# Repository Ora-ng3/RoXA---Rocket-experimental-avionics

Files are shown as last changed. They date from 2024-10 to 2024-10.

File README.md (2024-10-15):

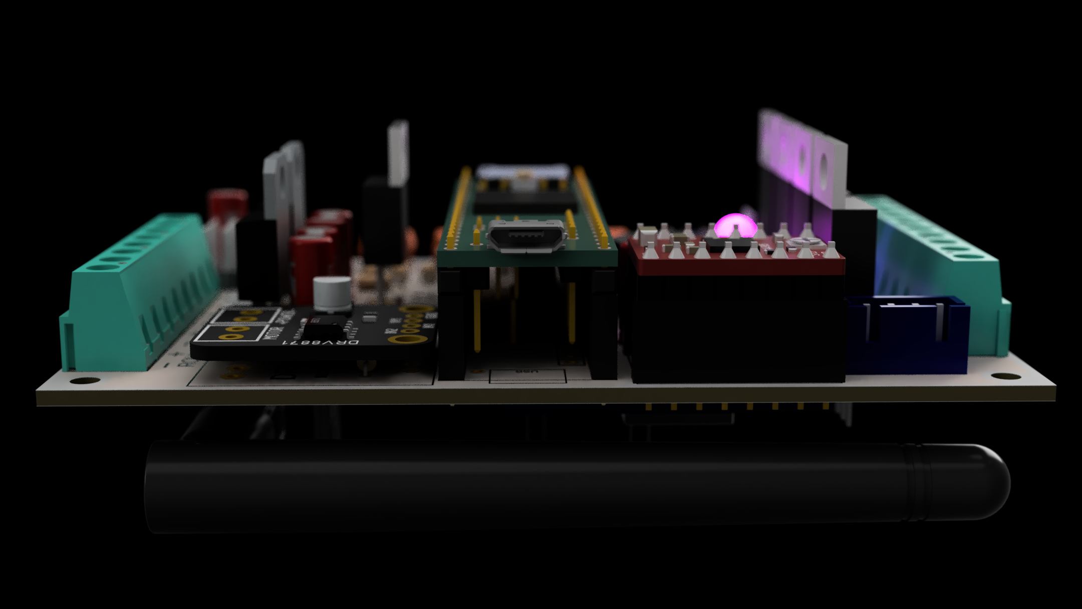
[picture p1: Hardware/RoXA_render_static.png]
The RoXA Flight Computer


RoXA stands for Rocket experimental avionics. It's my first flight computer (that is more than an arduino with a barometer soldered : ), you can see in [this instructables](https://www.instructables.com/Rocket-Flight-Computer/) a more detailed description of the design and build.

In this repo you'll find the PCB design and manufacturing files, as well as the code. For now it can reliably trigger first and second events. I'm working actively on this project to add reliable data logging and telemetry (and many other things...).

The RoXA Flight Computer

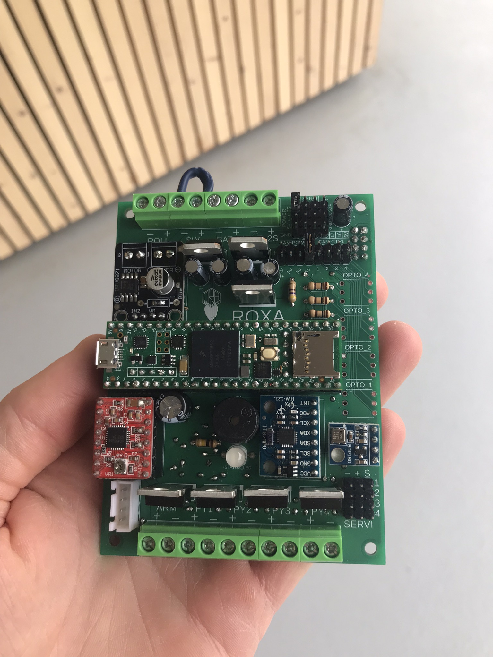
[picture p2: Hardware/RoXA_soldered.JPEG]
The RoXA Flight Computer


Keywords : Flight computer avionics Rocket Reaction wheel Rogallo

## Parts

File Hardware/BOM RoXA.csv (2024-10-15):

Qty | Device | Value | Parts | Unit Price | Price
1 | Microcontroller | Teensy 4.1 | U$1 | 40,00 € | 40,00 €
1 | Barometer | GY-68 BMP180 | U$4 | 2,00 € | 2,00 €
1 | IMU | GY-521 MPU6050 | U1 | 2,50 € | 2,50 €
1 | GPS | GY-NEO6MV2 | U$3 | 10,00 € | 10,00 €
1 | Radio Module | NRF24L01+PA+LNA | U$2 | 4,00 € | 4,00 €
1 | Motor Driver | DRV8871 | U$5 | 8,00 € | 8,00 €
1 | Stepper Driver | A4988 | U$6 | 2,00 € | 2,00 €
1 | RGB Led | 5mm Com. Cat. | STATUS_LED | 0,10 € | 0,10 €
1 | Buzzer | 3.3V 12mm | U$7 | 1,00 € | 1,00 €
2 | 5V Regulator | L7805CV TO220V | CAM_5V_REG, MAIN_5V_REG | 0,80 € | 1,60 €
5 | N-Mosfet | IRFZ44N TO220V | CAM_FET, PYFET1, PYFET2, PYFET3, PYFET4 | 0,80 € | 4,00 €
15 | Resistor | 100k | R2, R3, R4, R8, R9, R10, R14, R15, R16, R20, R21, R22, R26, R27, R28 | 0,05 € | 0,75 €
4 | Resistor | 1ohm | R5, R11, R17, R23 | 0,05 € | 0,20 €
1 | Resistor | 10ohm | R31 | 0,05 € | 0,05 €
2 | Resistor | 68ohm | R29, R30 | 0,05 € | 0,10 €
4 | Resistor | 100ohm | R33, R34, R35, R36 | 0,05 € | 0,20 €
5 | Resistor | 470ohm | R6, R12, R18, R24, R32 | 0,05 € | 0,25 €
5 | Resistor | 1M | R1, R7, R13, R19, R25 | 0,05 € | 0,25 €
2 | Capacitor | 1µF | C2, C7 | 0,15 € | 0,30 €
4 | Capacitor | 10µF | C1, C4, C5, C6 | 0,15 € | 0,60 €
1 | Capacitor | 100µF | C3 | 0,15 € | 0,15 €
4 | Optocoupler | 4N28 | OPTO_1, OPTO_2, OPTO_3, OPTO_4 | 0,15 € | 0,60 €
8 | Headers | 2 pins | CAM_BREAKOUTS | 0,01 € | 0,08 €
4 | Headers | 3 pins | SERVO_HD_1, SERVO_HD_2, SERVO_HD_3, SERVO_HD_4 | 0,01 € | 0,04 €
4 | Headers | 4 pins | POWER_BK | 0,01 € | 0,04 €
1 | Stepper connector | 4 pins JST XH | STEPPER_BK | 0,10 € | 0,10 €
9 | Screw terminals | 2 pins 5mm | ARM, BATT, BAT_2S, PY1, PY2, PY3, PY4, ROLL, SW | 0,10 € | 0,90 €
1 | PCB Board |  |  | 2,00 € | 2,00 €
 |  |  |  | Total : | 81,81 €

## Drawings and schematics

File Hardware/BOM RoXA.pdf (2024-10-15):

### BOM ROXA

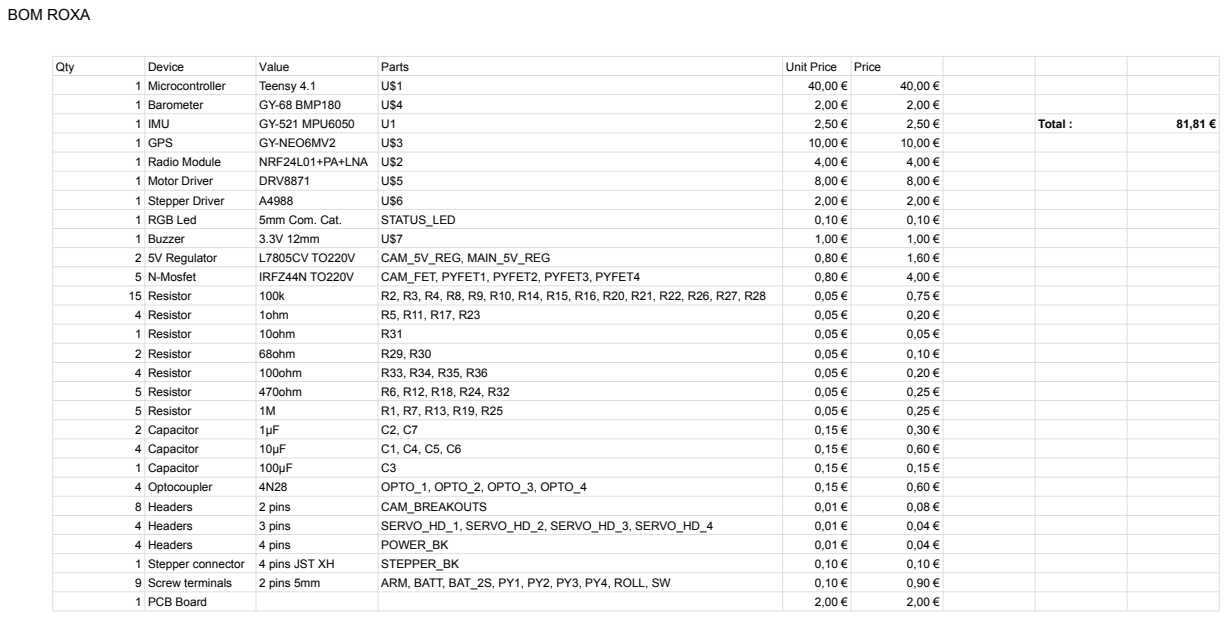
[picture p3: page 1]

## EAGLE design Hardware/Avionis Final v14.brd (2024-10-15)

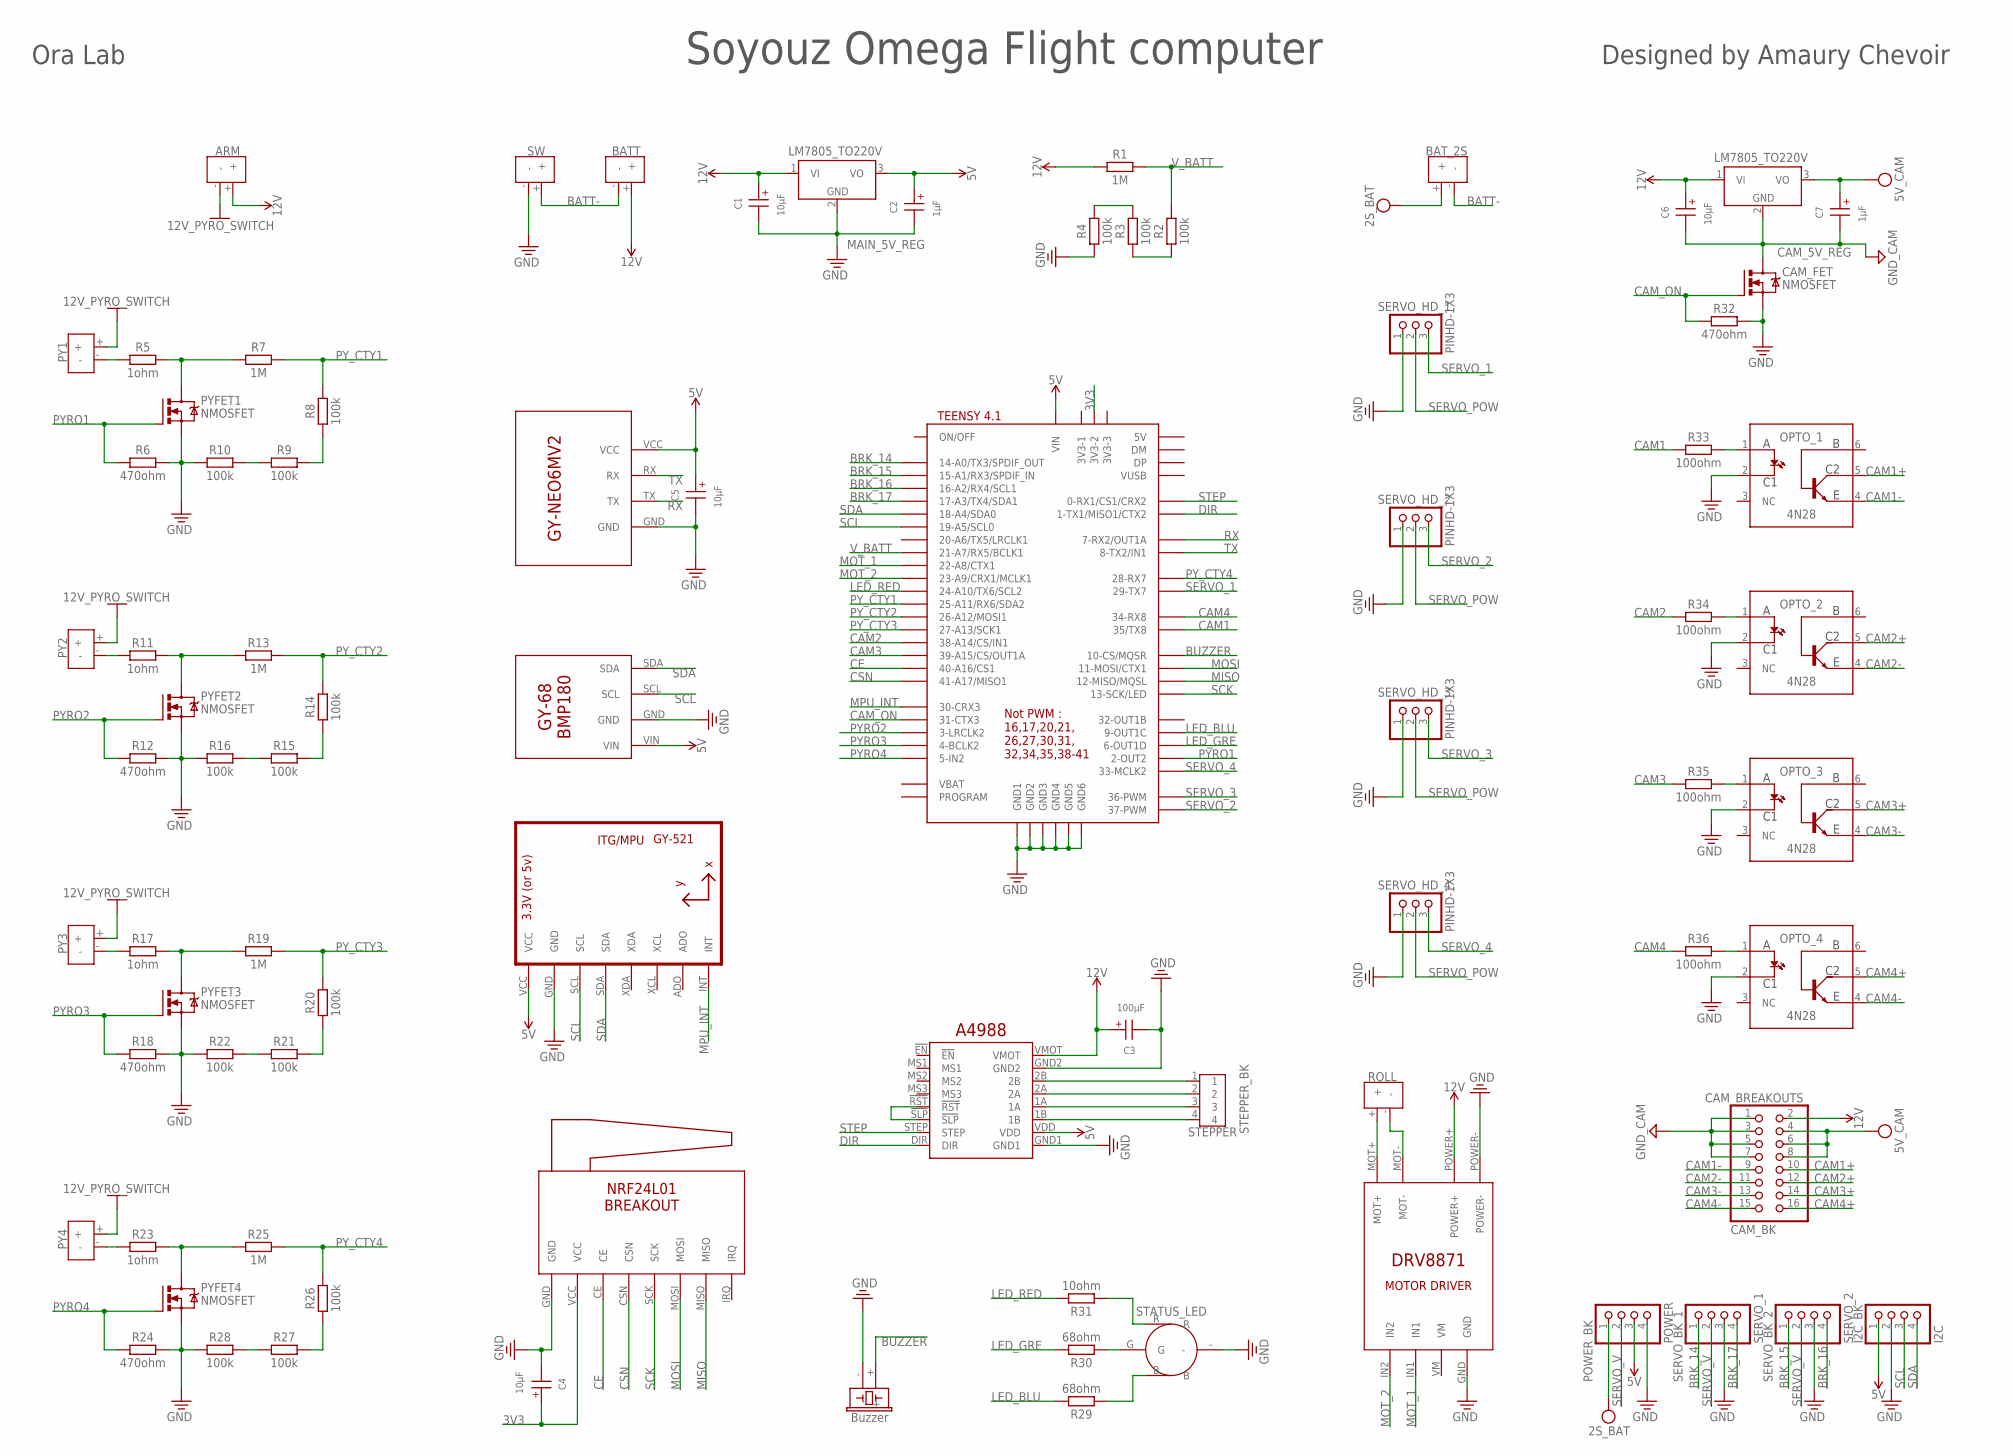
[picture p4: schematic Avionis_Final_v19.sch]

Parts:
ARM: TERMBLK_2; TERMBLK_2_LOW
BATT: TERMBLK_2; TERMBLK_2_LOW
BAT_2S: TERMBLK_2; TERMBLK_2_LOW
C1, C4, C5, C6: 10µF; WCAP-AT1H_5X11(DXL)
C2, C7: 1µF; WCAP-AT1H_5X11(DXL)
C3: 100µF; WCAP-AT1H_5X11(DXL)
CAM_5V_REG: LM7805_TO220V; TO220V
CAM_BREAKOUTS: CAM_BK; 2X08
CAM_FET: NMOSFET; TO220BV
I2C_BK: I2C; 1X04
MAIN_5V_REG: LM7805_TO220V; TO220V
OPTO_1, OPTO_2, OPTO_3, OPTO_4: 4N28; DIP762W60P254L712H480Q6B
POWER_BK: POWER; 1X04
PY1, PY2, PY3, PY4: TERMBLK_2; TERMBLK_2_LOW
PYFET1, PYFET2, PYFET3, PYFET4: NMOSFET; TO220BV
R1, R7, R13, R19, R25: 1M; RESAD724W46L381D178B
R2, R3, R4, R8, R9, R10, R14, R15, R16, R20, R21, R22, R26, R27, R28: 100k; RESAD724W46L381D178B
R5, R11, R17, R23: 1ohm; RESAD724W46L381D178B
R6, R12, R18, R24, R32: 470ohm; RESAD724W46L381D178B
R29, R30: 68ohm; RESAD724W46L381D178B
R31: 10ohm; RESAD724W46L381D178B
R33, R34, R35, R36: 100ohm; RESAD724W46L381D178B
ROLL: TERMBLK_2; TERMBLK_2_LOW
SERVO_BK_1: SERVO_1; 1X04
SERVO_BK_2: SERVO_2; 1X04
SERVO_HD_1, SERVO_HD_2, SERVO_HD_3, SERVO_HD_4: PINHD-1X3; 1X03
STATUS_LED: LED_RGB_CAT_THT
STEPPER_BK: STEPPER; B4B-XH-A
SW: TERMBLK_2; TERMBLK_2_LOW
U1: GY-521MPU6050; GY-521
U$1: TEENSY41-E; TENNSY41-E
U$2: NRF24L01_BREAKOUT
U$3: GY-NEO6MV2
U$4: GY-68_BMP180
U$5: DRV8871_MOTORDRIVER
U$6: A4988
U$7: BUZZER_12MM; BUZZER-12MM-KIT

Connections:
1A: STEPPER_BK.3, U$6.1A
1B: STEPPER_BK.4, U$6.1B
2A: STEPPER_BK.2, U$6.2A
2B: STEPPER_BK.1, U$6.2B
2S_BAT: BAT_2S.+, POWER_BK.1
3V3: C4.1 (+), U$1.3V3-2, U$2.VCC
5V: C2.1 (+), C5.1 (+), I2C_BK.1, MAIN_5V_REG.3 (VO), POWER_BK.3, U1.VCC, U$1.VIN, U$3.VCC, U$4.VIN, U$6.VDD
5V_CAM: C7.1 (+), CAM_5V_REG.3 (VO), CAM_BREAKOUTS.4, CAM_BREAKOUTS.6, CAM_BREAKOUTS.8
12V: ARM.+, BATT.+, C1.1 (+), C3.1 (+), C6.1 (+), CAM_5V_REG.1 (VI), CAM_BREAKOUTS.2, MAIN_5V_REG.1 (VI), R1.1, U$5.POWER+, U$6.VMOT
12V_PYRO_SWITCH: ARM.-, PY1.+, PY2.+, PY3.+, PY4.+
!RST: U$6.!RST, U$6.!SLP
BATT-: BATT.-, BAT_2S.-, SW.+
BRK_14: SERVO_BK_1.1, U$1.14-A0/TX3/SPDIF_OUT
BRK_15: SERVO_BK_2.1, U$1.15-A1/RX3/SPDIF_IN
BRK_16: SERVO_BK_2.4, U$1.16-A2/RX4/SCL1
BRK_17: SERVO_BK_1.4, U$1.17-A3/TX4/SDA1
BUZZER: U$1.10-CS\MQSR (10-CS/MQSR), U$7.+
CAM1: R33.1, U$1.35-TX8 (35/TX8)
CAM1+: CAM_BREAKOUTS.10, OPTO_1.5 (C2)
CAM1-: CAM_BREAKOUTS.9, OPTO_1.4 (E)
CAM2: R34.1, U$1.38-A14/CS/IN1
CAM2+: CAM_BREAKOUTS.12, OPTO_2.5 (C2)
CAM2-: CAM_BREAKOUTS.11, OPTO_2.4 (E)
CAM3: R35.1, U$1.39-A15/CS/OUT1A
CAM3+: CAM_BREAKOUTS.14, OPTO_3.5 (C2)
CAM3-: CAM_BREAKOUTS.13, OPTO_3.4 (E)
CAM4: R36.1, U$1.34-RX8
CAM4+: CAM_BREAKOUTS.16, OPTO_4.5 (C2)
CAM4-: CAM_BREAKOUTS.15, OPTO_4.4 (E)
CAM_ON: CAM_FET.G, R32.1, U$1.31-CTX3
CE: U$1.40-A16/CS1, U$2.CE
CSN: U$1.41-A17/MISO1, U$2.CSN
DIR: U$1.1-TX1/MISO1/CTX2, U$6.DIR
GND: C1.2 (-), C2.2 (-), C3.2 (-), C4.2 (-), C5.2 (-), CAM_FET.S, I2C_BK.2, MAIN_5V_REG.2 (GND), OPTO_1.2 (C1), OPTO_2.2 (C1), OPTO_3.2 (C1), OPTO_4.2 (C1), POWER_BK.4, PYFET1.S, PYFET2.S, PYFET3.S, PYFET4.S, R4.1, R6.2, R10.1, R12.2, R16.1, R18.2, R22.1, R24.2, R28.1, R32.2, SERVO_BK_1.3, SERVO_BK_2.3, SERVO_HD_1.1, SERVO_HD_2.1, SERVO_HD_3.1, SERVO_HD_4.1, STATUS_LED.-, SW.-, U1.GND, U$1.GND1, U$1.GND2, U$1.GND3, U$1.GND4, U$1.GND5, U$1.GND6, U$2.GND, U$3.GND, U$4.GND, U$5.GND, U$5.POWER-, U$6.GND1, U$6.GND2, U$7.-
GND_CAM: C6.2 (-), C7.2 (-), CAM_5V_REG.2 (GND), CAM_BREAKOUTS.1, CAM_BREAKOUTS.3, CAM_BREAKOUTS.5, CAM_BREAKOUTS.7, CAM_FET.D
LED_BLU: R29.2, U$1.9-OUT1C
LED_GRE: R30.2, U$1.6-OUT1D
LED_RED: R31.2, U$1.24-A10/TX6/SCL2
MISO: U$1.12-MISO/MQSL, U$2.MISO
MOSI: U$1.11-MOSI/CTX1, U$2.MOSI
MOT_1: U$1.22-A8/CTX1, U$5.IN1
MOT_2: U$1.23-A9/CRX1/MCLK1, U$5.IN2
MPU_INT: U1.INT, U$1.30-CRX3
unnamed: ROLL.+, U$5.MOT+
unnamed: ROLL.-, U$5.MOT-
unnamed: PY2.-, R11.1
unnamed: PYFET2.D, R11.2, R13.1
unnamed: R15.1, R16.2
unnamed: R14.1, R15.2
unnamed: PY3.-, R17.1
unnamed: PY1.-, R5.1
unnamed: R9.1, R10.2
unnamed: PYFET1.D, R5.2, R7.1
unnamed: R2.1, R3.1
unnamed: R3.2, R4.2
unnamed: R8.1, R9.2
unnamed: PYFET3.D, R17.2, R19.1
unnamed: R21.1, R22.2
unnamed: R20.1, R21.2
unnamed: PY4.-, R23.1
unnamed: PYFET4.D, R23.2, R25.1
unnamed: R27.1, R28.2
unnamed: R26.1, R27.2
unnamed: R30.1, STATUS_LED.G
unnamed: R31.1, STATUS_LED.R
unnamed: OPTO_1.1 (A), R33.2
unnamed: R29.1, STATUS_LED.B
unnamed: OPTO_2.1 (A), R34.2
unnamed: OPTO_3.1 (A), R35.2
unnamed: OPTO_4.1 (A), R36.2
PYRO1: PYFET1.G, R6.1, U$1.2-OUT2
PYRO2: PYFET2.G, R12.1, U$1.3-LRCLK2
PYRO3: PYFET3.G, R18.1, U$1.4-BCLK2
PYRO4: PYFET4.G, R24.1, U$1.5-IN2
PY_CTY1: R7.2, R8.2, U$1.25-A11/RX6/SDA2
PY_CTY2: R13.2, R14.2, U$1.26-A12/MOSI1
PY_CTY3: R19.2, R20.2, U$1.27-A13/SCK1
PY_CTY4: R25.2, R26.2, U$1.28-RX7
RX: U$1.7-RX2/OUT1A, U$3.TX
SCK: U$1.13-SCK/LED, U$2.SCK
SCL: I2C_BK.3, U1.SCL, U$1.19-A5/SCL0, U$4.SCL
SDA: I2C_BK.4, U1.SDA, U$1.18-A4/SDA0, U$4.SDA
SERVO_1: SERVO_HD_1.3, U$1.29-TX7
SERVO_2: SERVO_HD_2.3, U$1.37-PWM
SERVO_3: SERVO_HD_3.3, U$1.36-PWM
SERVO_4: SERVO_HD_4.3, U$1.33-MCLK2
SERVO_POW: SERVO_HD_1.2, SERVO_HD_2.2, SERVO_HD_3.2, SERVO_HD_4.2
SERVO_V: POWER_BK.2, SERVO_BK_1.2, SERVO_BK_2.2
STEP: U$1.0-RX1/CS1/CRX2, U$6.STEP
TX: U$1.8-TX2/IN1, U$3.RX
V_BATT: R1.2, R2.2, U$1.21-A7/RX5/BCLK1

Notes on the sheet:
Soyouz Omega Flight computer
Ora Lab
Designed by Amaury Chevoir

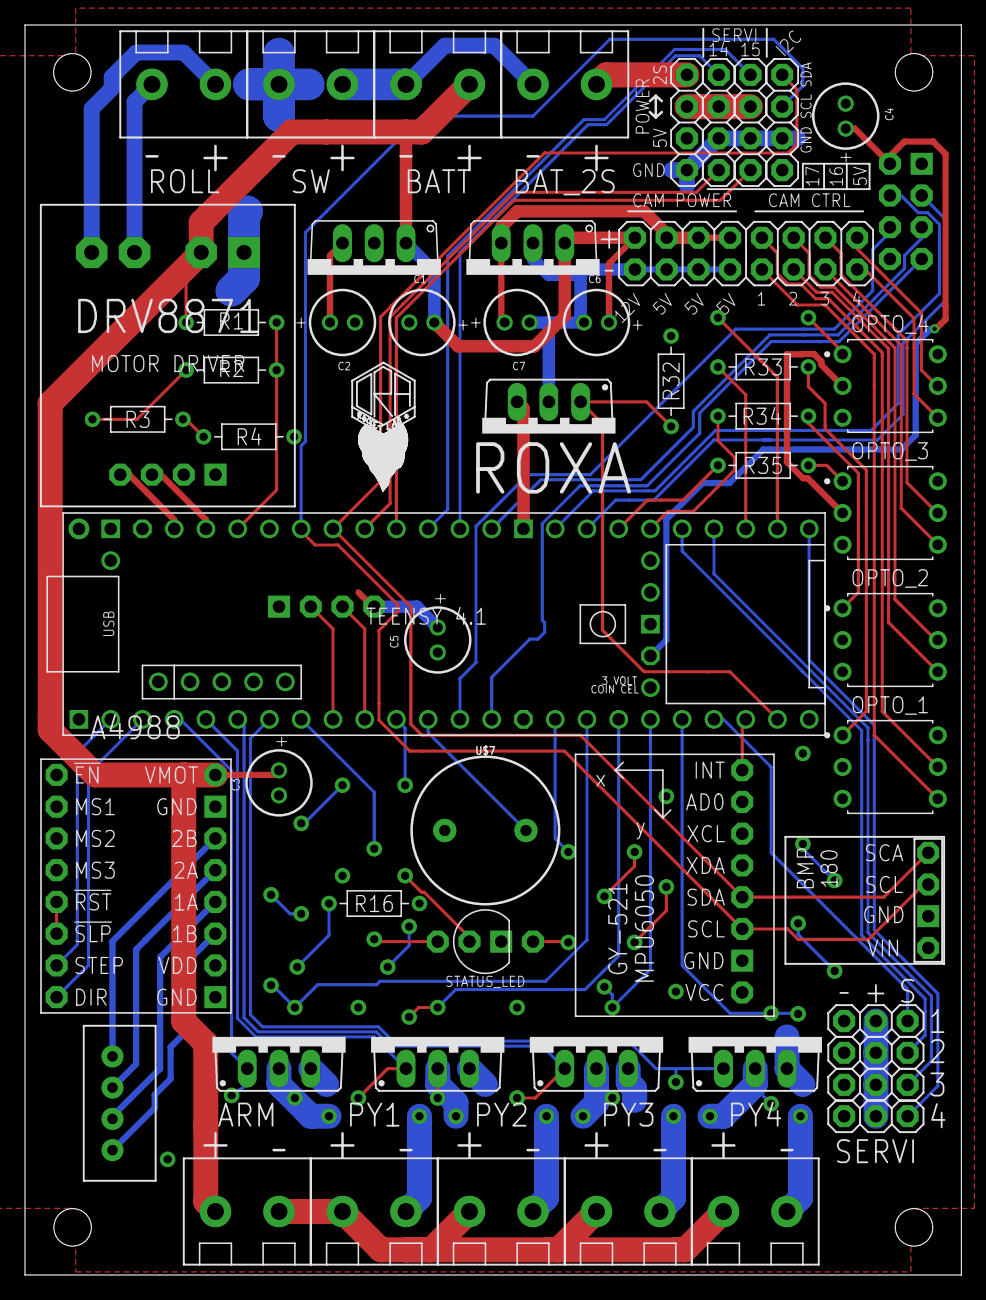
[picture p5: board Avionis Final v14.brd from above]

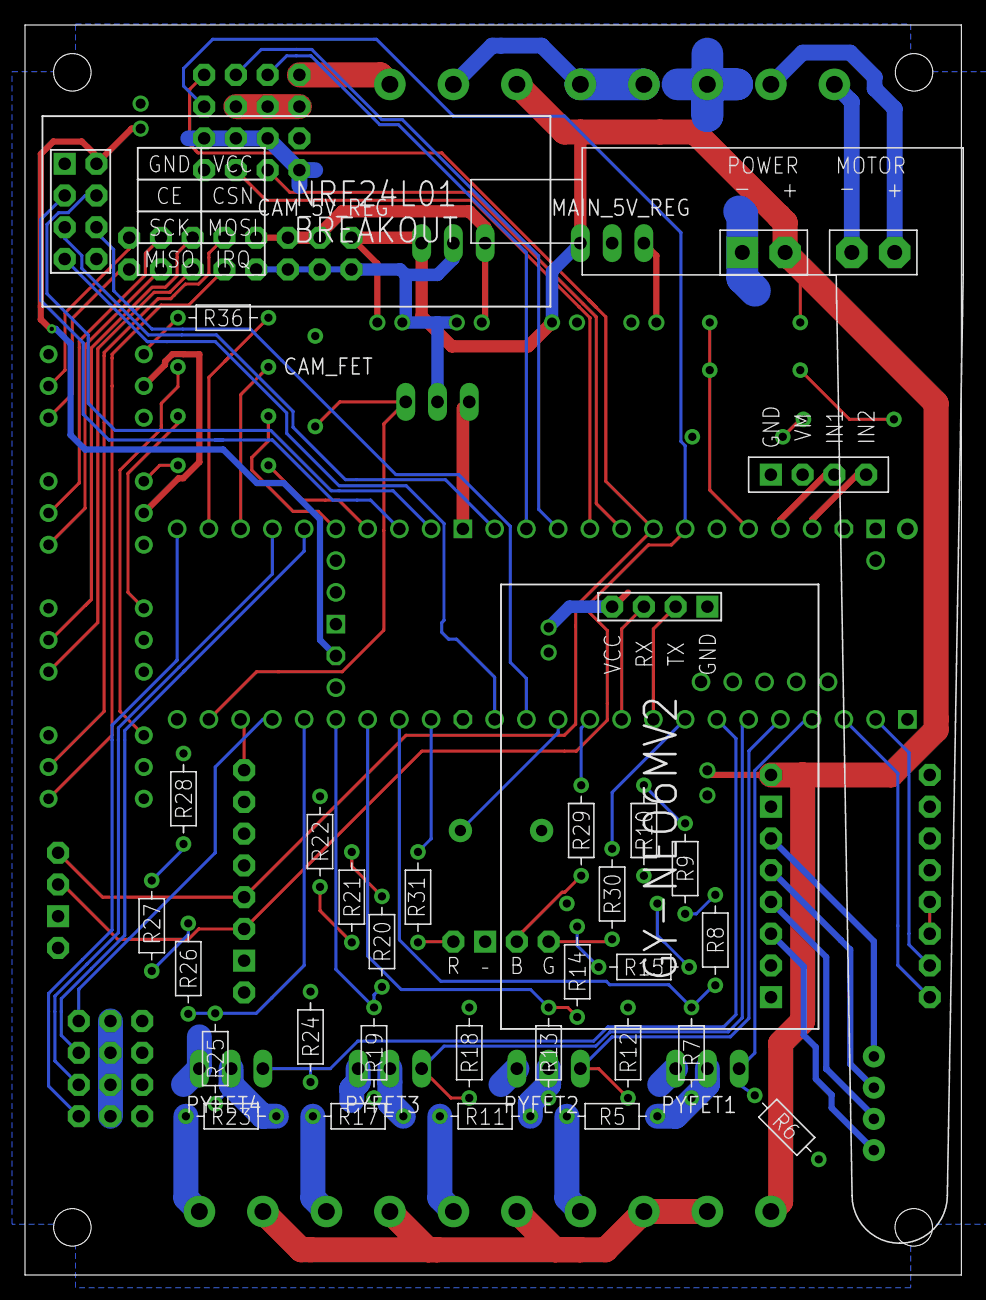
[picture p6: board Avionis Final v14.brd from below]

Board: 2 copper layers, 74.9 x 100.0 mm, 82 parts (29 on the bottom side), 91 nets.

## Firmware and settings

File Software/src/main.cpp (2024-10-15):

#include <Arduino.h>
#include "FC.h"

void setup() {
    Serial.begin(9600);
	Serial.println("Starting setup");

	FC = new FlightComputer();
	FC->initialize();

	setupComplete(); // show that setup is complete
	FC->set_state(IDLE);
	// timeStepUpdate();
}

void loop() {
	FC->readSensors();
	//massManager();

	FC->navigate(); // where is the rocket ? (position, velocity, attitude)
	//guidance(); // where do we want to go ?
	FC->control(); // how do we get there ?

	//inFrameComms(); // sends and receives data so next events can be trigerred

	FC->eventManager(); // checking trigger functions and time constraints
	Pyro::manager(); // manages PYRO objects, checks for continuity and, if firing
					 // checks durations
	FC->memoryManager(); // sometimes writes data to flash memory (no PSRAM ?)
	timeStepUpdate(); // ensures 100Hz rate
}

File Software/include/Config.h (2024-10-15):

// dimensions, expected apogee, expected deploy delay, main deploy altitude
// main deploy consec frames (nb of frames where conditions have to be met)
// apogee minimum time (min tome since liftoff to check for apogee)

//#define PSRAM
//#define FLASH
#define SD_LOG
//#define FINE_ACC_GYRO_CALIBRATION
//#define CANSAT
#define REACTION_WHEEL

#define GyroXOffset 82
#define GyroYOffset -18
#define GyroZOffset 56
#define AccelXOffset -927
#define AccelYOffset -273
#define AccelZOffset 953

#define SLOW_LOG_RATE 1 // Hz
#define FAST_LOG_RATE 10 // Hz

#define FPS 10 // Hz

#define BARO_DROP 5 // m
#define BARO_ASCENDING_TRIGGER 5 // m
#define BARO_MAIN_DEPLOY 200 // m

#define LED_BRIGHTNESS 0.1

//#define TEST

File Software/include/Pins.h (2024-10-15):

// Pin definitions for ROXA
#ifndef PINS_H
#define PINS_H

constexpr int STEP = 0;
constexpr int DIR = 1;
constexpr int PYRO1 = 2;
constexpr int PYRO2 = 3;
constexpr int PYRO3 = 4;
constexpr int PYRO4 = 5;
constexpr int LED_B = 6;
constexpr int RX = 7;
constexpr int TX = 8;
constexpr int LED_G = 9;
constexpr int BUZZER = 10;
// MOSI = 11
// MISO = 12
//constexpr int SCK = 13; (already defined in core_pins.h from teensy)
constexpr int BRK_14 = 14; // Top
constexpr int BRK_15 = 15; // Bottom
constexpr int BRK_16 = 16;
constexpr int BRK_17 = 17;
// SDA = 18
// SCL = 19
// 20 : unused (A6, TX5, LRCLK1)
constexpr int BATT = 21;
constexpr int MOT_1 = 22;
constexpr int MOT_2 = 23;
constexpr int LED_R = 24;
constexpr int PYRO_CTY1 = 25;
constexpr int PYRO_CTY2 = 26;
constexpr int PYRO_CTY3 = 27;
constexpr int PYRO_CTY4 = 28;
constexpr int SERVO_1 = 29;
// 30 : unused (CRX3)
// 31 : unused (CTX3)
// 32 : unused (OUT1B)
constexpr int SERVO_4 = 33;
constexpr int CAM_4 = 34;
constexpr int CAM_1 = 35;
constexpr int SERVO_3 = 36;
constexpr int SERVO_2 = 37;
constexpr int CAM_2 = 38;
constexpr int CAM_3 = 39;
constexpr int NRF_CE = 40;
constexpr int NRF_CSN = 41;

#endif

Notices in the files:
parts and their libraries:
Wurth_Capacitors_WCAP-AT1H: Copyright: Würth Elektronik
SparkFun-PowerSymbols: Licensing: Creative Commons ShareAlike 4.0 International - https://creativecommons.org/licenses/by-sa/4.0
